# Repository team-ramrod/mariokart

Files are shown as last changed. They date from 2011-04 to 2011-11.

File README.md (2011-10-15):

MarioKart
=========

The full description of this project can be found on our [github wiki](https://github.com/team-ramrod/mariokart/wiki)

Purpose
-------

To retrofit one of the EE department's electric go-karts with a drive by wire
system, controllable over a single USB interface. Add to this a simple example
of a closed-loop controller using sensors and software running on a \*nix
laptop.

Method
------

Control the electric motor, servo driven steering wheel and actuated brake
pedal via embedded arm microprocessors. The separate micros are connected via a
CAN and also leave room for an arbitrary number of analog and digital sensors.

Behavioural-level software runs on a laptop connected to this network via USB.

Future Work
-----------

Develop a more complete sensor network (possibly including computer vision in
collaboration with cosc428) alongside more advanced controller software.

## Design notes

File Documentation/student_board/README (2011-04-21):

This is the source code for the student board running a ATmega8 on the go kart.
It was given to us by Bill
It also includes the schematic for the pcb.

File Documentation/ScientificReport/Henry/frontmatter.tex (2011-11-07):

\title{Embedded Hardware Design For An Autonomous Electric Vehicle}

\author{
  \IEEEauthorblockN{
    Henry Jenkins \\
    \href{mailto:hvj10@uclive.ac.nz}{\texttt{hvj10@uclive.ac.nz}}
  }

  \vspace{0.5\baselineskip}

  \IEEEauthorblockN{
    \emph{Coauthors}: Simon Richards, Zachary Taylor, Wim Looman and Dr Andrew Bainbridge-Smith\\
    \href{mailto:scr52@uclive.ac.nz}{\texttt{scr52@uclive.ac.nz}}
    \href{mailto:zjt14@uclive.ac.nz}{\texttt{zjt14@uclive.ac.nz}}
    \href{mailto:wgl18@uclive.ac.nz}{\texttt{wgl18@uclive.ac.nz}}
    \\\href{mailto:andrew.bainbridge-smith@canterbury.ac.nz}{\texttt{andrew.bainbridge-smith@canterbury.ac.nz}}
  }

  \vspace{0.5\baselineskip}

  \IEEEauthorblockA{
    Department of Electrical and Computer Engineering\\
    University of Canterbury\\
    Christchurch, New Zealand
  }
}

\maketitle

\begin{abstract}
  This report details the design and production of a hardware platform to for
  an autonimous go-kart. The system includes seven printed circuit boards
  (PCBs).  Five of the PCBs communicate via a CAN bus to collect data and
  control other circuitry, while the other two PCBs control actuators for
  steering and brake control. The system is based around Atmel AT91SAM7XC micro
  controllers along with various other electronics. The PCBs built for this
  system  are four layers so were manufactured in America by Advanced Circuits,
  then populated and tested at the University of Canterbury.
\end{abstract}

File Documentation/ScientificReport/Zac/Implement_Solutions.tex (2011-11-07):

\section{Implementation of Solutions}

Colour detection, SURF and chessboard detection were all implemented to evaluate their performance for tracking a marker in the required environment. To aid in this implementation extensive use was made of the Opencv computer vision libraries \cite{opencv}. These libraries were used as they contained implementations of a large number of computer vision algorithms that had been thoroughly tested by a large community and optimized to run as effectively and efficiently as possible.

The first algorithm implemented was the simple colour based approach. In this approach a bright blue ball was used as the marker to track. Initially the scene was thresholded for a value that was approximately a bright blue and opening (that is erosion followed by dilation) was used to fill any holes in the image of the ball and remove background noise. The output of this process can be seen in Figure~\ref{ball}. A rough estimation of the balls location was then made using its x and y position in pixels from the centre of the camera. The z location of the ball was taken to be proportional to the inverse of the square root of the size of the ball in pixels. These measures of x, y and z were extremely crude however they provided adequate for the testing that was performed on the colour method.

\begin{figure}[ht]
	\begin{center}
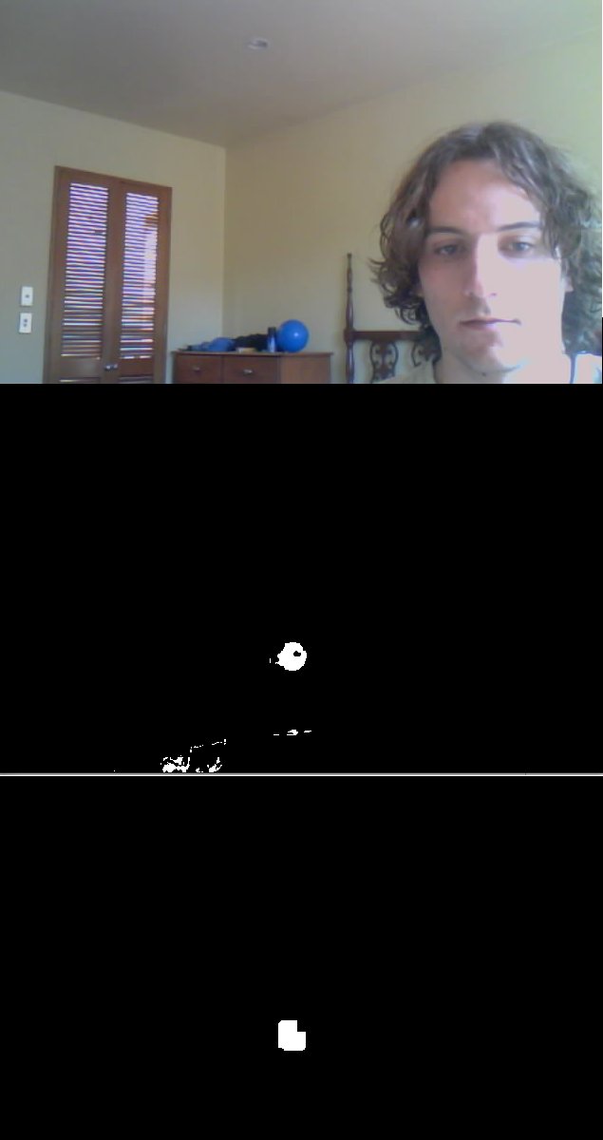
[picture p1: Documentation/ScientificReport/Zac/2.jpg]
		
	\end{center}
	\caption{Detection of marker ball using colour}
	\label{ball}
\end{figure}

For both the SURF and chessboard algorithms the intrinsic parameters of the camera had to be found so that the size of an object on the screen could be translated from the arbitrary pixel co-ordinate system used by the images to real world distances. These parameters were found by using the camera to take a series of photos of the chessboard from different angles and distances and using the geometry of the chessboard to extract the cameras parameters \cite{cali}. Once this had been performed the parameters were saved to a file that was used by both algorithms. This calibration was a small disadvantage of these algorithms however as it only had to be performed once for a web-cam it did not diminish the practicality of their use by much.

The SURF algorithms marker was a printout of a cut away of an aeroplane. This image was used as it contained a large amount of strong lines and detail that meant that a large number of unique and easily identifiable points could be located on the image. An example of the SURF algorithm working can be seen in Figure~\ref{plane}. 

Two chessboards were constructed and tested with the chessboard registration algorithm. A large 6 by 5 chessboard with 100 mm squares and a smaller 7 by 8 chessboard. The larger chessboard was to be used with the kart once it was running. The smaller one was used for calibrating the camera and the testing covered in this report. The smaller board can be seen being used in Figure~\ref{tracking}. 

\begin{figure}[ht]
	\begin{center}
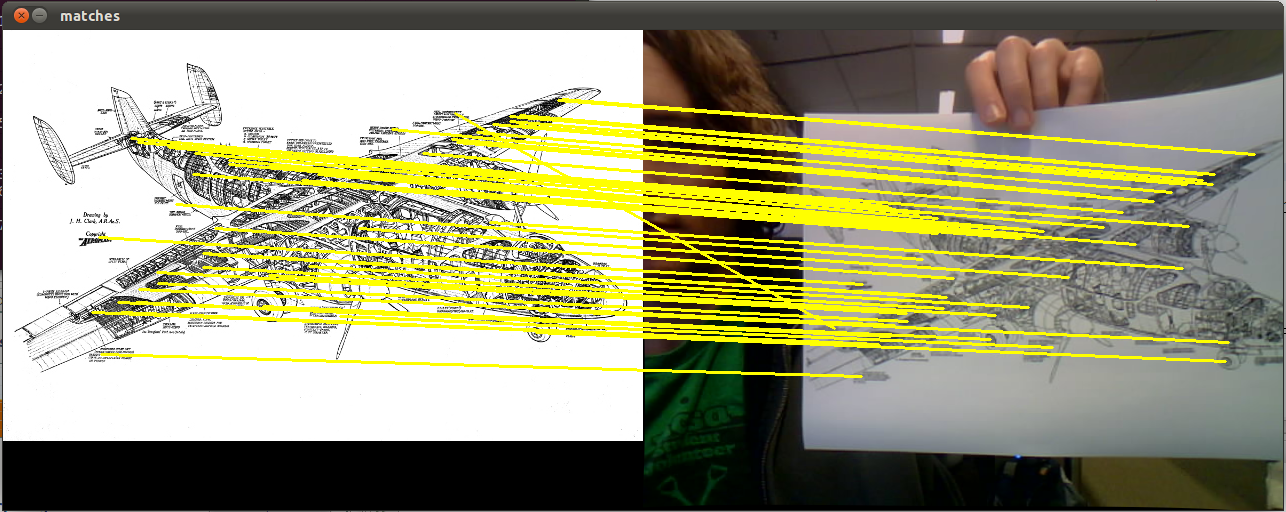
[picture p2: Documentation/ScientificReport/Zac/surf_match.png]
		
	\end{center}
	\caption{The SURF algorithm matching points in the marker image to the scene}
	\label{plane}
\end{figure}

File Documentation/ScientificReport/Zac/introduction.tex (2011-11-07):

\section{Introduction}

An electric go-kart was to be converted to allow it to navigate autonomously. To this end the system, nicknamed Mariokart was being modified so that it could be controlled from a laptop. This control system required a program to be written which would give the kart some basic autonomous functionality. This program was to function as a proof of concept of the kart's abilities as well as a method to test the systems that had been added to the kart. It had been decided that this program should allow the kart to follow a marker. 

The system that was being designed allowed the systems on the kart to interface through a laptop to 5 boards located on different areas of the kart. These boards handled all the low level control of the kart providing the laptop with functions to set the steering, brake and accelerator position. It also provided functions to access sensors located on the kart through fairly high level commands. The only sensor present on the kart at the start of the development was a speed sensor however a large number of I/O ports of different types allowed for the addition of extra sensors.  

The developed program was to run on the on-board laptop. It had to operate in real time recognizing the marker, finding its location and outputting the path to travel on with minimal lag. The kart was expected to be able to operate in both indoor and outdoor environments in a large variety of conditions without losing the marker. The system and any additional equipment and sensors required had to be low budget as the total budget for the entire conversion was less than \$1500.

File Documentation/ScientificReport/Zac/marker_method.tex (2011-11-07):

\section{Marker Location Methods}

A large variety of location methods were looked at when determining what type of sensors should be purchased for the kart system. Most modern autonomous vehicles rely heavily on scanning laser sensors as their main method of viewing the surroundings. Scanning lasers as their name implies rapidly move a measuring laser over the environment forming a matrix of distances to provide a 3D view of the world \cite{laser}. While these lasers are extremely useful they were discounted as a possibility early due to their high price tag with even the most basic models starting at \$2000. The Microsoft Kinect camera was briefly looked at as an alternative solution that would provide 3D information about the world \cite{kinect}. This camera uses structured light combined with an IR (inferred) camera to detect the location of objects in its field of view. This system was also quickly discounted however as it had a maximum range of only 3.5m which was too limiting for the application of tracking a marker from on board a kart. A second aspect that counted against the Kinect was that the IR pattern used by it was washed out by direct sunlight making outdoor use impractical.

GPS systems, while briefly examined as a possibility were not given any serious consideration due to their inability to work reliably in an indoor environment. One solution that was given serious consideration was using a marker that output a RF (radio frequency) signal and having three RF receivers on the kart use the  relative strength of the signal to triangulate the position of the marker. After further research it was found however that distance estimation using the level of RF detectors that were within the budget was only accurate to around 1m under ideal conditions \cite{rf}. This limitation meant that the receivers would have to be placed far apart to minimize the effect the error would have on the direction the triangulation would calculate the signal to have come from. On a mobile kart system where the close proximity of the sensors was unavoidable this limitation made the method infeasible.

The sensor system that was decided upon to develop was a computer vision system. This system utilized a web-cam mounted to the front of the kart. A unique marker was to be used that could be located in the image. This method had several advantages over the other methods considered. It was a cheap and easy to mount solution with only a web-cam required that would attach straight to the laptop with a USB cable. It provided a large degree of flexibility with a large suite of different algorithms and methods able to be implemented and tested for no modifications to the hardware the system was using. Finally it was the only system that showed promise in being able to locate a marker accurately at distance and within the budget. It was for these reasons that the computer vision system was the only option pursued for development.

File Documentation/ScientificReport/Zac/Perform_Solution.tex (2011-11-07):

\section{Performance of Solutions}
The algorithms were put through a series of tests to guage how well they would perform in the system. All the tests were performed on a 2.1 GHz notebook with an Intel Centrino Duo processor. The webcam was a Creative Labs Laptop Integrated Webcam. This webcam had a resolution of 320 by 240 pixels and operated at 20 fps.

\subsection{Robustness to lighting}
The robustness to light was tested by setting up an algorithm to recognise its marker in a room with a large amount of natural light. The lighting was then changed by closing the curtains and seeing if the object was still detected, once this was done the rooms lights were turned on. Colour detection performed the worst in this test requiring recalibration before it could detect the target after every change in lighting. Its robustness could be improved but this caused issues with background noise, this is gone into in detail in subsection E. The issue  with lighting arose because while the hue of the marker being located remained constant changing the lighting levels altered the hue the camera perceived the marker to be by a small amount. This problem stemmed right from the fundamental method by which the camera detects light and so very little could be done without recalibrating to attempt to account for this change \cite{detect}. The SURF algorithm handled almost all lighting changes without issue. The one situation in which it failed was if enough glare was coming off the marker it was locating to completely obscurer most of the features it was trying to find. The chessboard algorithm worked under every tested lighting condition.

\subsection{Frame processing speed}
The FPS (frames per second) for each system was recorded under normal operation. The colour detection algorithm required easily the least processing power of all the computer vision methods looked at running at a solid 20 fps only limited by the speed of the camera it was receiving the images from. The SURF algorithm operated very slowly originally operating at 0.8 FPS on locating a 640 by 480 pixel reference image in the scene. This speed was increase to 2 FPS by decreasing the reference image to 320 by 240. This was the lowest quality reference image which could be reliably placed in the scene. Chessboard detection operated slowly if the chessboard had not been located in the previous frame only operating at a rate as low as 2 fps. Once the chessboard was found however the algorithm used the previous location to find it more quickly raising the frame rate to around 15 fps.

\subsection{Robustness to motion}
Robustness to motion was tested in a fairly subjective manner. The marker was held roughly 1m from the camera and shaken until detection was lost. With colour detection regardless of how fast the marker was moved detection was never lost, though the detected size decreased by up to around 50\% as the image of the marker became a blur. With SURF detection only slow and careful movements would prevent the camera losing the target. Chessboard detection would lose the board if any quick or jerky movements were made. While this test was quite crude it clearly showed that SURF would be too susceptible to motion blur to be appropriate. It also showed that chessboard detection was weak to it and a higher quality camera or some pre-processing might be needed to help reduce the effect of motion blur when the system is attached to the kart.

\subsection{Maximum distance for detection}
The maximum distance the algorithm could detect a marker from was tested next. To make this a fair test for all systems the marker size for each system was set to an A4 page with the colour detections blue ball replaced by a sheet of blue card. The test was performed by walking away from the camera holding the marker and recording the distance at which the target was lost for the first time. The process was repeated three times and the results shown in Table~\ref{dist}. SURF performed easily the poorest of the solutions with the marker needing to take up a large portion of the field of view of the camera before recognition occurred. The chessboard algorithm lost the board at around 3m. At this point the 2.5cm squares on the board were only around 3 pixels in height and so little more in terms of performance could be expected from the algorithm. The colour detection operated up to 10 m at which point the marker was so small on the camera that it was removed as noise during opening. All three algorithms only operated over a relatively short distance in comparison to how far the kart might be from the marker. This would mean that the actual marker to be tracked would need to be significantly larger then those used in testing and/or a higher resolution camera would have to be used.

\begin{table}
	\caption{Distance before detection of marker is lost (all values in meters).}
	\begin{center}
    	\begin{tabular}{ | l | l | l | l | l |}
    	\hline
    	Algorithm & Run 1 & Run 2 & Run 3 & Average \\ \hline
		Colour & 10 & 11.5 & 9 & 10.2 \\ \hline
		SURF & 1.0 & 0.7 & 1.1 & 0.9 \\ \hline
		Chessboard & 3.5 & 3.0 & 3.2 & 3.2 \\ \hline
    	\end{tabular}
	\end{center}
	\label{dist}
	
\end{table}

\subsection{Robustness to background noise}
The ability of the algorithm to operate on a variety of backgrounds was tested. How much the colour detection was effected was closely coupled to how well it performed in varying light. If the range of hues and saturations was set to be very close to the markers colour then almost no issues with background objects occurred. An example of this can be seen in Figure~\ref{ball} where the blue ball is detected while sitting next to a blue can and a blue towel with neither of these being detected. These close tolerances meant that lighting had to be kept almost constant for the marker to be detected. If these ranges were relaxed to work in more varying light then any similarly coloured part of the background would also be detected. The SURF algorithm also had issues with the background. When the image was being tracked a small amount of the points (usually less than 10\%) would be attributed to points in the background. These incorrect points did not affect the algorithm however as the RANSAC algorithm detected them for the outliers that they were. The main issues came when the image was far away, partly obscured or absent from the scene. In these situations a large number of points would be detected at locations in the background giving false positives for locations of the marker. These locations were almost always easy to detect as they usually claimed that the marker was hundreds of meters away however they still required filtering and subtracted from the robustness of SURF. The chessboard was almost completely unaffected by the background. This was because while on occasion a false corner point was detected as it did not match the structure of the rest of the points it was discarded without problem. This lead to no false positives as for a chessboard to be perceived when not present, 42 false points would have to be located in a structure that very closely resembeled that of the chessboard.

\subsection{Accuracy of distance measurement}
The accuracy of the distances given was tested by placing the marker at 3 different points and recording the error of the system. These measurements are shown in Table~\ref{acc}. The SURF detection performed poorly in this test having an average error of 18\%. It also failed to register on the 2 meters test performing easily the worst of the three. Chessboard detection was almost as accurate as the tape measure being used to compare the distances giving a maximum error of only 1.5\%. Colour detection performed far better than expected given its crude distance calculation method having an error of only 6.8\%. Something that must be taken into account however is that the colour detection is in reality less accurate then this test indicated. This is because the amount of the marker detected depends on the lighting conditions and the distance was calculated using size of the marker. This meant turning on a light could change the distance the process believed the marker was at by a large amount (20\% in one rough test).

\begin{table}
	\caption{Accuracy of distance measurements}
	\begin{center}
    	\begin{tabular}{ | p{1.1cm} | p{0.5cm} | p{0.6cm} | p{0.5cm} | p{0.6cm} | p{0.5cm} | p{0.6cm} | l |}
    	\hline
    	Algorithm & \multicolumn{2}{|c|}{At 0.5m} & \multicolumn{2}{|c|}{At 1m} & \multicolumn{2}{|c|}{At 2m} & Avg \\ \hline
    	& Value & Error & Value & Error & Value & Error & \\ \hline
		Colour & 0.57 & 14.0\% & 1.03 & 3.0\% & 2.07 & 3.5\% & 6.8\% \\ \hline
		SURF & 0.61 & 22.0\% & 1.14 & 14.0\% & - & - & 18.0\% \\ \hline
		Chessboard & 0.495 & 1.0\% & 0.99 & 1.0\% & 1.97 & 1.5\% & 1.2\% \\ \hline
    	\end{tabular}
	\end{center}
	
	\label{acc}
	
\end{table}

\subsection{Testing conclusions}
From these tests it was concluded that chessboard detection was the only algorithm that was appropriate for use on the kart. This was because SURF was too sensitive to motion blur and had too short a range for the application. While colour detection out performed chessboard detection in several areas its sensitivity to light changes meant that it would never be robust enough to be useful.

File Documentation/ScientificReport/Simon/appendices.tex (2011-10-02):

\section{Appendices}

\subsection{Promela examples}
Client Board proctype:
\lstinputlisting[language=Promela]{client.pml}

\pagebreak
Never claim: All boards transition to error state
or remain in running state indefinitely:
\lstinputlisting[language=Promela]{never.pml}

\subsection{Single board state machine}

\begin{figure}[!ht]
  \caption{The state machine each board follows.}
  \label{states}
  \centering
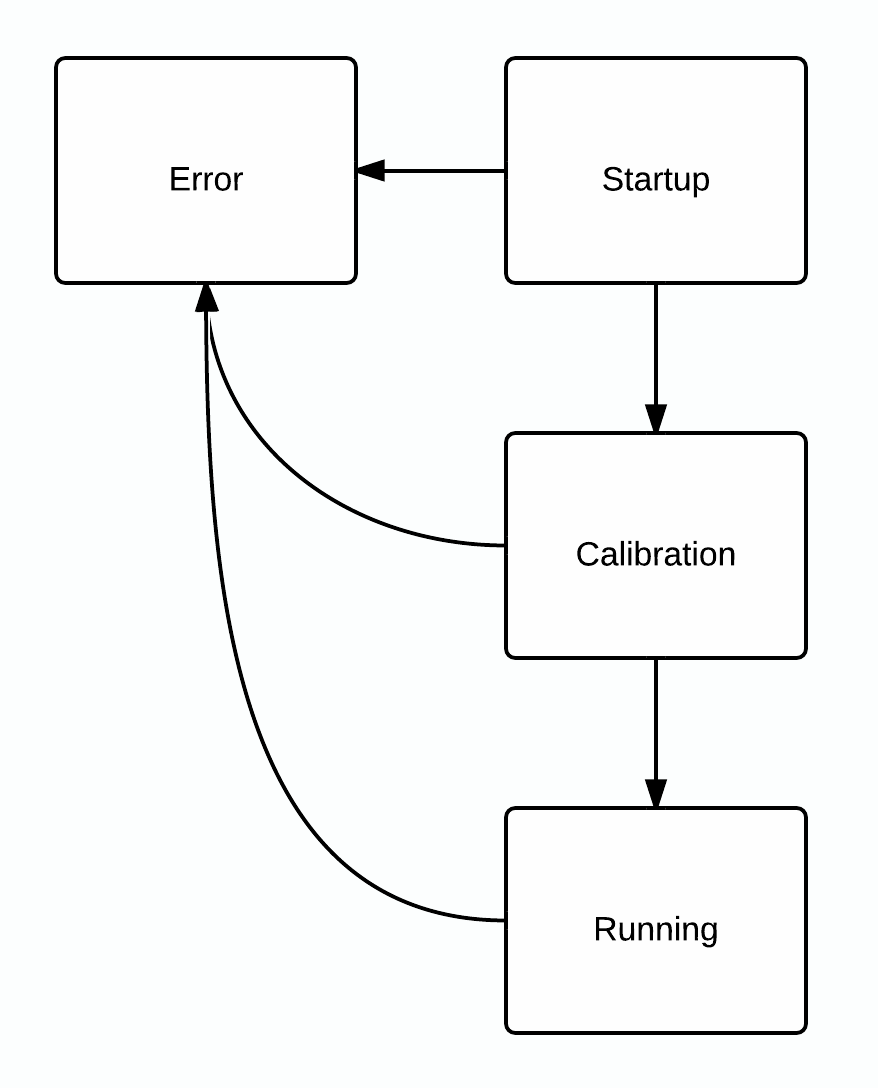
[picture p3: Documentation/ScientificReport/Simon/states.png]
    
\end{figure}

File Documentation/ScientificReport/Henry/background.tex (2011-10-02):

\section{Background}
  To interface to the go-kart, actuators were required to be placed at both the
  front of the kart, as well as interfacing to the power electronics in the
  rear.

\subsection{The Go-kart}
  The department has 5 electric go-karts that were purchased for the specific
  purpose of a assignment and project platform, one of these shown in Fig.
  \ref{go-kart}. Throughout the year several, mostly power electronics,
  assignments are based on the Junoir Sport JS80IIR go-kart\cite{go-kart}. These
  go-karts are 1.7 meters in length, can hold two passengers and came with a
  80cc petrol motor. The petrol motor has since been replaced with a DC electric
  motor and batteries.

  \begin{figure}[h]
      \centering
      
      \caption[Junoir Sport - JS80IIR go-kart]{Electrical and Computer
      Engineering go-kart}
      \label{go-kart}
  \end{figure}

\subsection{Power Supply}
  The go-kart has a single power source for the whole vehicle. Two lead-acid
  batteries provide power for the existing DC drive motor and power electronics.
  These batteries can handle large currents at a voltage ranging up to 26 volts.
  The batteries have also been made accessible to be used for the autonomous
  vehicle control system.

\subsection{Power Electronics}
  To control the DC Drive motor, the department has designed and built three
  PCBs to switch and regulate currents going through the motor. Figure
  \ref{powerE} shows the three PCBs, where from left to right they are known as
  the \emph{student board}, \emph{control safety board} and \emph{power
  electronics board}. The \emph{student board} is a 5V logic board that takes
  the position of the accelerator pedal, current sensor data and outputs a PWM
  signal for the \emph{control safety board}. The control safety board is there
  to make sure the \emph{power electronics board} is not incorrectly driven,
  which would damage the go-kart.

  \begin{figure}[h]
      \centering
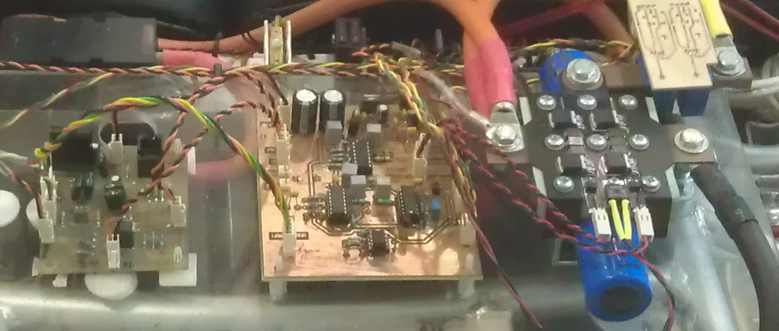
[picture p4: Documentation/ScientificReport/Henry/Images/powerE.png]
      
      \caption{Power and control electronics for go-karts DC motor}
      \label{powerE}
  \end{figure}

\subsection{Actuator Control}
  To control the steering position and apply the brakes two actuators were
  purchased for the project.

  \subsubsection{Steering}
    The steering motor is a 24V DC motor that has a step down gear box with an
    output ratio of 393:1. On the top end of the motor, there is a magnetic
    encoder\cite{encoder} that outputs 18 pulses per motor revolution. This is that it outputs
    7,074 pulses per 360 degrees of rotation on the steering wheel. At peak
    load, the steering motor can draw up to 10Amps continuously.

  \subsubsection{Brake}
    To control the position of the brake a linear actuator is used. The linear
    actuator has an extension of 101.6mm and can travel at 20mm/s. It provides
    absolute position feedback via a $10k\ohm$ potentiometer. As with the
    steering motor, the brake linear actuator ran at 24V but only draws a peak
    current of 1.3Amps.

\subsection{Communication With A Laptop}
  Because most laptops have dropped all serial RS-232 ports, the only reliable
  option for serial communications is to use USB.

\subsection{Schematic \& PCB design tools}
  To generate the PCBs and schematics, Altium Designer was used\cite{altium}.
  Altium Designer is a complex electronics design package that can be used from
  a variety of tasks. However in this project only the schematic layout and PCB
  design tools were used.

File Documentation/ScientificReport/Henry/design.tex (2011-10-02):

\section{Design}
  To avoid problems of running long signal wires, especially near the large DC
  go-kart motor, it was decided to distribute the electronic control hardware.
  This also has the benefit that the system is extensible including being able
  add new sensors later on with plenty of spare IO spread around the kart.

  To make the design simpler and cheaper the same design was used for all the
  main PCBs. Just not populating certain components where they are un-nessary.
  For example, the USB connector was only placed on the \emph{comms board} as it
  is the only board that requires to talk to a computer.

  \subsection{Board locations}
  To prevent long runs of digital logic in the go-kart there were five PCBs
  placed around the go-kart. The locations of the boards are:
  \begin{itemize}
  \item Steering - Placed where the steering wheel is, next to the steering
  actuator.
  \item Brake - Directly next to the brake actor where the brake pedal normally
  is.
  \item Comms - On the go-kart seat with the laptop next to it.
  \item Motor - Connected to the power electronics controlling the main DC motor
  \item Sensor - Near the rear axle collecting speed data from the inductance
  sensor.
  \end{itemize}
  Figure \ref{locations} shows a sketch of where the PCBs are located.

  \begin{figure}[h]
    \centering
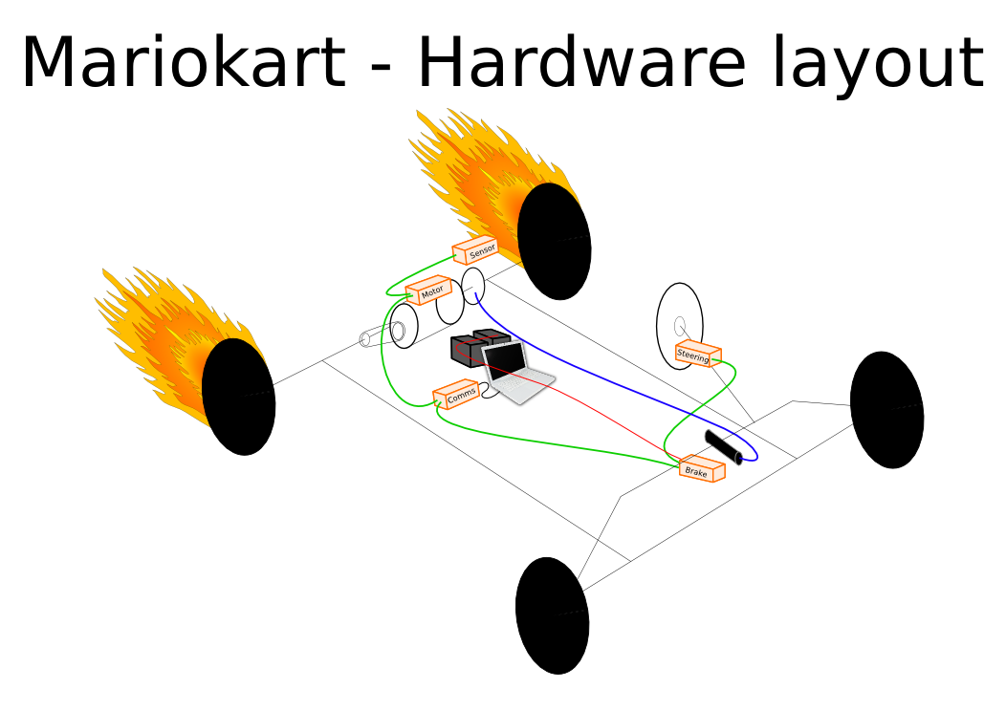
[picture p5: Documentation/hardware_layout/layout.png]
    
    \caption{Locations of PCBs for go-kart}
    \label{locations}
  \end{figure}

  \subsection{Communications Network}
  Because the go-kart was required to be controlled by distributed hardware,
  some way of having the hardware communicate was required. To solve this
  problem, Local Interconnect Network (LIN Bus), Controller Area Network (CAN
  Bus), Universal Asynchronous Receiver/Transmitter (UART) and Serial
  Peripheral Interface Bus (SPI) were evaluated as viable options. Both LIN and
  CAN are serial communication buses designed for use in vehicle and automation
  systems, where UART and SPI are designed as simple serial communications.
  
  \begin{itemize}
    \item[LIN]{LIN is a single wire communications standard which supports
    speeds of up to 19.2kbit/s\cite{LIN}. It is a master slave design which
    supports up to sixteen slaves. The data frame on the LIN Bus is variable
    length of either 2, 4 or 8 bytes. There is no collision detection, however
    data checksumming and error detection is implemented in the standard.  LIN
    was designed in 1999 with further LIN standards released in 2002 and 2003.}

    \item[CAN]{CAN 2.0 is a master-master broadcast serial bus standard. It
    supports half-duplex data rates of up to 1Mbit/s. The CAN Bus uses a
    differential pair with the traffic encoded in non return to zero. Each
    packet is formatted with a header, including receivers address, followed by
    zero to eight bytes of data. Robert Bosch GmbH \cite{bosch} developed the
    standard in 1983, but now days the ISO11989 standard also describes CAN 2.0
    \cite{boschCAN, ISOCAN}.}

    \item[UART]{Using UART was dropped as an idea rather early on. This is
    because it does not support the error correction that was needed for the
    project. Another area it was lacking is being expandable. A new UART would
    be required for each new node or device.}

    \item[SPI]{For much the same reasons UART was not used for our central
    communications bus, SPI was also not appropriate.} 

  \end{itemize}

  It was decided that using a CAN Bus would be the best option. Some major
  factors that influenced this choice over LIN were; the CAN standard had better
  documentation, more nodes can be added to the network later on with little
  extra effort, hardware level collision and error detection and CAN controller
  supported by Atmel SAM7 series micro controller. Atmel also provided a CAN
  transceiver IC\cite{ata666}, however this could have been replaced by a IC
  made by Texas Instruments\cite{ti-can-trans}.

  Although both UART and SPI were not used for the system bus, both can be used
  for local sensors, or other expansion modules.

  \subsection{Micro Controller}
  The main requirements of the micro controller are that it supports both a CAN
  controller and hardware USB. Also because previous projects had used either
  the Atmel ATMega or the Atmel AT91SAM7 micro controllers, it was of preference
  to use these rather than learning a new architecture and data sheet format.

  \subsection{Motor Drivers}
  To drive the actuators for the steering and brake we decided to use a motor
  driver IC. By basing our motor driver circuit specification on the current
  draw of the steering motor, then reused the same design for the brake linear
  actuator we could use the same circuit for both actuators. This was done both
  to save time in the hardware design, but also time in software later
  on\cite{Looman_2011}. The motor driver circuits were placed on their own small
  PCB to save space on the main PCBs and also provide more opportunity for heat
  dissipation if this were to become a problem. 

  The motor driver that was used is the DRV8432 made by Texas
  Instruments\cite{ti-motor-driver}. It is a dual full bridge PWM motor driver.
  It has a split logic and driving voltage, so it is driven directly from the
  batteries, but the control logic is at 3.3V. It has a peak voltage of 50V and
  a maximum current of 12A which is more than we need for either of the
  actuators. Figure \ref{motorPCB} shows one of the two motor driver boards with
  a heat sink covering the motor driver IC.

   \begin{figure}[h]
     \centering
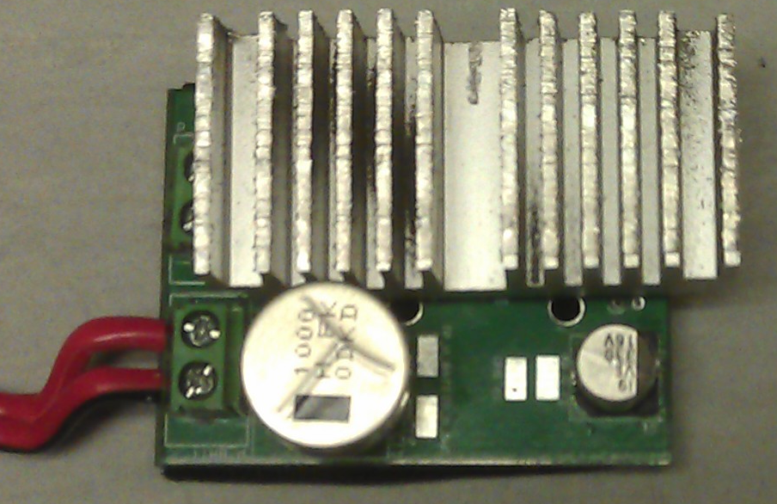
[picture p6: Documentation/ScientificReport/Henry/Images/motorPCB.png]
     
     \caption{Motor driver board for driving actuators}
     \label{motorPCB}
   \end{figure}

  \subsection{Expansion IO}
  To allow the hardware to be expandable, two 3.3V UARTs, one 3.3V SPI and
  one 5V logic SPI are exposed on each PCB. Each serial port has it's own
  PicoBlade connector\cite{PicoBlade} as well as all the power supplies are
  exposed via another connector. All the serial port pins can also be set to be
  GPIO to allow them to be used for other purposes too.

  The 5V logic SPI is enabled via the use of a logic level shifter chip
  the MAX3001E made by Maxim \cite{MAX3001E}. To complement the 5V spi, a 5V
  external ADC is also on the boards. This was placed on the boards for the
  purpose of replacing the student board, but can be used for other analogue
  input too.

  \subsection{Encoder Reading}
  Because getting both speed and directions from an encoder signal in software
  is quite tricky, a quadrature clock converter was placed on the main steering
  PCB.  This takes in the encoder pulses and out puts a single pulse and which
  direction it is rotating in. Which allows a simple counter and incrementing or
  de-incrementing it to keep the actuators position.

  \subsection{Debugging}
  To make debugging easier, epically in the early stages of development, a two
  digit seven segment display and 4 push buttons are placed on each main PCB. The
  display is driven by a display driver. This display driver takes a four bit
  number in parallel and converts it into the segment array lines. It is
  multiplexed with the second segment so by switching between the displays
  faster than 20Hz allows both digits can be used.

  \subsection{On Board Power}
  On each board there is four different voltage five levels. There is the
  battery voltage, which is only used by the voltage regulators, 3.3V, 5V, 12V
  and ground. Because we used a 4 layer PCB design, excluding the battery
  voltage, each of the voltage levels were spread across a whole plane on the
  PCB allowing better coupling between them and ground.

    \subsubsection{3.3 Volts}
    This was used by most of the logic components including the SAM7 micro
    controller. As less than 300mA was required and having a smooth, non-rippled,
    voltage would ensure the micro controller ran well, a linear voltage
    regulator was used.

    \subsubsection{5 Volts}
    The main reason for having 5 volts on the boards was to allow a 3.3V to 5V
    logic translator to be used. This level shifter is required by the student
    board in the power electronics. A linear voltage regulator was used here
    also.

    \subsubsection{12 Volts}
    Both the inductance sensor, which is used for speed detection, and the motor
    driver required 12 volts. Both of these applications use less than 150mA so
    a Texas Instruments TPS7A4901 linear voltage regulator was
    used \cite{TPS7A4901}.

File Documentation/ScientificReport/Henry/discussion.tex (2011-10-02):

\section{Discussion}
 In general the design process produced good stable and usable boards. However
 there were a few areas that needed improving on.

\subsection{Debug Port}
  When the schematic was being set out the debug unit from the SAM7 were left
  with no header leading to them. At the time it was thought that they would be
  unnecessary and then were forgotten about. This meant all the debugging was
  required to be done via a UART port and the display. While this wasn't a bad
  solution to the problem, it would have been better to have access to the debug
  unit.

\subsection{Test points}
  At the last minute in the PCB design about 100 test points were added to the
  bottom of the PCB. This was very useful and one of the better design decisions
  with the PCB. The test points gave access to many different signals on the
  board with test point probes able to be clipped onto them. The only thing that
  should be done differently with the test points is placing more ground test
  points around the board. This would allow more than one oscilloscope cable to
  be hooked up to the ground on the board.

\subsection{Power Supply Selector}
  Making the decision to put battery voltage over the same cables that the CAN
  bus uses made the system work well. However when developing and debugging, it
  would have been ideal to be able to disconnect the power coming in from the
  CAN bus cable. This would mean that an individual board could be power cycled
  without having to power cycle all of them. This could have been done by simply
  putting two jumpers on the PCBs to connect specific ones to enable either the
  CAN bus power or the battery header power.

\subsection{Connectors}
  To save space the Molex Pico Blade \cite{PicoBlade} connectors were used.
  However after using them this was a bad choice. They are very hard to make
  cables for, then brake a short time after. This is frustrating when it takes
  so long to make them, yet they don't last long. While using bigger more
  traditional connectors would have taken up more space on the PCBs, it would
  have saved a lot of time while developing with the boards.

%\subsection{Atmel Library}
  % You suck atmel

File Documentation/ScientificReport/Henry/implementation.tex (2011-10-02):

\section{Implementation}
  The Main PCBs are four layer PCBs that were designed using Altium software.
  They are approximately 120mm long by 60mm wide.

  \subsection{Schematics}
  Using Altium Designer the schematics were laid out. Two techniques were used
  to minimise mistakes in the PCB design. One was to divide all the schematic
  sections onto separate sheets. The other was to be methodical and make notes
  on the sheets if something was not complete. Part of being methodical also
  meant making sure all components were well labelled, even some with comments
  next to them to help explain their existence. This meant when the schematics
  were printed off and reviewed by the whole team, mistakes could be easily
  spotted.
  
  \begin{figure*}[h]
      \centering
      
      \caption{Top level schematic for the main PCB.}
      \label{main-schematic}
  \end{figure*}

  Figure \ref{main-schematic} shows the top level schematic with the MCU in the
  middle of the page. The green boxes on the sheet show where other sub sheets
  have been included and wired up. For example, doing this all the decoupling
  capacitors for the micro controller are essentially hidden in one of these
  sub sheets. 

  \subsection{PCB Design}
  The PCB layout design work was also done in Altium Designer. While the tool
  does not automatically do the layout for the user, it does provides many
  useful tools to aid the process. By setting up the design rules to match the
  manufactures specifications, the manufacture process is sped up eliminating
  them rejecting your design because of design rule violations.

  The main technique that was used when laying out the PCB was to arrange
  clusters of components that are all related. Then place these modules on the
  PCB area. This also allowed the placing of decoupling capacitors in the
  correct locations next to the pin that required the decoupling.
  
  One key rule that was stuck to when laying the PCB was to only put small
  components on the bottom. This allowed the population of the whole bottom side
  of the PCBs then when populating the top side, the components would not fall
  off the bottom in the oven. It also meant we could fit the PCBs in the lid of
  the enclosure that we designed the boards to fit in. The small resistors and
  capacitors don't even touch the inside of the lid.

  \subsection{Components}
  Where possible surface mount technology (SMT) components were selected. This
  has the benefit that it minimises the amount of drilling required to be done
  by the manufacturer. It is also easier to source SMT components. In the final
  design only some connectors are non-SMT.

  \subsection{PCB Manufacture}
  To allow four layer PCBs to be used, the PCBs needed to be manufactured
  off-shore. Because of recommendations by staff in the department, either
  Advanced Circuits in America\cite{advancedCircuits} or OurPCB Tech in
  China\cite{ourPCB} were our best options.  Because of price, Advanced Circuits
  were used. All up for 3 panels, which included all 5 main PCBs and two motor
  driver daughter boards, the charge was 362 USD including shipping. The panels
  were manually cut into the individual PCBs, using a band saw.
  
  \subsection{PCB Population}
  Component population was done initially using a PCB oven, then
  reverting back to hand soldering once the bulk of the components were on the
  PCBs. Population was done in stages, to allow testing of the boards at each
  stage. Figure \ref{fullPCB} shows the brake PCB with all it's components on
  it.
  
  \begin{figure}[h]
      \centering
      
      \caption{The populated brake PCB}
      \label{fullPCB}
  \end{figure}

  \subsection{Hardware Testing}
  Before the PCBs even had any components put on them they were tested for
  manufacturing and design flaws. Simply using a multi meter, checking to make
  sure the power planes were not shorted and other key pads were connected as
  they should have been. Then continued to be tested at every stage especially
  making sure the power and ground planes were not shorted was a key concept. At
  several stages shorted pins were picked up because of this testing.

  Once the PCBs had their micro controller placed on its PCB, led test code was
  written to ensure we were able to program and control the board. This also
  helped to pick up shoddy soldering on a couple of the micro controllers. The
  same was repeted for the CAN Bus, push buttons and USB.

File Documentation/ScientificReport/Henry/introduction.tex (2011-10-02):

\section{Introduction}
% Goal / problem statement (what is your goal/what problem are you solving)
  Currently the department of Electrical and Computer Engineering at the
  University of Canterbury has several go-karts. These go-karts were purchased
  as petrol go-karts then retrofitted with control electronics, power
  electronics, lead-acid batteries and a DC electric motor. The goal of this
  project was to take one of these existing electric go-karts and have it drive
  it's self autonomously. 

  An autonomous vehicle is a driver-less vehicle that is able to navigate from
  one location to another set location by controlling actuators and motors. This
  is achieved by gathering data from the surrounding environment in order to
  find and track the vehicle's current location. While the vehicle can have
  communications off the vehicle, like off loading signal processing, it is
  ideal to have the vehicle completely self contained. This, however, does not
  dismiss using incoming radio signals. For example using Global Positioning
  System (GPS) would be perfectly acceptable.

  The control systems, both mechanical and electrical, must interface with
  existing hardware on the go-kart. The project aimed to select appropriate
  actuators, motion and distance sensors, develop a navigation system, interface
  to the existing control systems and interface to a central computing platform.
  As the kart also was required for other projects, it was also a requirement to
  able return the kart to it's initial electric go-kart state within an hour.

  To be able to drive a go-kart autonomously, first the kart must be able drive
  according to given digital instructions. So the initial milestone is to build
  embedded hardware systems that is able to control the go-kart's main motor and
  drive actuators for both the brake and steering. Because the time line of this
  project spans approximately only 24 weeks, a sub-goal was set of having
  \emph{drive-by-wire} go-kart by the end of the project.

  To allow high performance, high level signal processing the control system
  must be able interface to a computer based platform. This platform will be
  able to run processor intensive tasks, like image processing for computer
  vision\cite{openCV}, or a Bayes filter for estimating the kart's current
  location before it receives accurate sensor data.

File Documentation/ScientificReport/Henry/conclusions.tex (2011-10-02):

\section{Conclusions}
  The design process used for the schematic and PCB layout worked well providing
  a set of very functional and reliable PCBs. They have been shown to all
  communicate together via the CAN Bus protocol and drive both the steering and
  brake actuators. 

  Since the project has been in the software development stage for some time
  now, there have only been three mistakes in the hardware found. All of these
  mistakes have had relatively easy fixes. The worst of the three is one side of
  the quadrature clock converter's pins were reversed. This was fixed by
  soldering the IC on upside down and then wiring the pins over to the correct
  pins. The second worst was a miss placed decoupling capacitor on the
  \emph{avref} pin of the SAM7. This was simply replaced with a zero ohm
  resistor to solve the problem. The third problem was that the UART connectors
  don't have a ground pin. To get around this the \emph{sclk} pin in tied low in
  software to act as a ground.

  Using the same design for all of the five main PCBs worked well. Doing this
  saved time in the design, ordering and population. This also saved money by
  being able panellise the boards which would have cost 50 USD more if wasn't
  done. By not having to spend time on making five different designs, more time
  was able to be spent checking for mistakes in the design. If there were
  multiple designs more mistakes would have happened.

  The CAN Bus produced clean signals with all nodes connected. Even with the CAN
  bus running at 1Mb/s its maximum speed. While the bandwidth of the CAN Bus is
  about 1000 times more than required for the current application of a
  drive-by-wire go-kart, it does mean the CAN bus can be expanded for future
  use with sensors and other devices generating traffic on the network. If noise
  were to become a problem, the bus is able to run at a slower rate potentially
  solving this issue.
  \newpage

  The help received from Michael Cusdin made this project possible. His
  knowledge and experience guided us through the PCB population process. Also
  technical knowledge provided by Dr Michael Hayes often lead us out of strife
  with challenging problems.

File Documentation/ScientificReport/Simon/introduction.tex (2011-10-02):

\begin{abstract}
An electric go-kart is outfitted with a drive-by-wire system in the first phase of development of 
an autonomous vehicle. The safety aspects of the design are evaluated and analysed  
using typical project management techniques. A model of the distributed software required is 
developed and proven and the place of modelling in software engineering is discussed..
\end{abstract}

\section{Introduction}

\subsection{Project Description}

The authors' reports are based on a group project carried out in the final year 
of their Bachelor of Engineering degree at Canterbury University. The original goal 
of this project was to take one of the electric go-karts used by the department for
power electronics projects and convert it into an autonomous vehicle capable of
a simple navigation task. Due to time restrictions the aim was reduced to implementing
the mechanical and electronic systems needed to control the kart's motion over a USB link.

The authors refer to the project using the moniker Mariokart and this name may be used 
throughout this report in reference to the team, the vehicle or the project itself.

\subsection{System Design}
The overall system design consisted of a laptop, electronics, a CAN bus, actuators and an interface to 
the existing motor driver  hardware.

\begin{itemize}
 \item Electronics: Five PCBs were located around the kart, each in close proximity to 
 the sub-system it was responsible for. The PCBs were identical in layout, specialisation was
 achieved by removing components from boards where they were not needed. For example
 it was intended for only one board to communicate directly with a laptop and so the other
 boards did not have USB headers. The decision to distribute control was made primarily to avoid
 problems caused by driving motors and actuators over a long distance in a high noise environment.
 \item Actuators: The brake pads were driven by a linear actuator mounted in place of the brake pedal. 
 The actuator was mounted to the floor of the go-kart and its driver board was situated nearby. The 
 steering column was similarly controlled by a DC motor mounted in place of the steering wheel 
 and fixed to the frame. The DC motor included an encoder so that the relative angle of the 
 steering column could be determined. Limit switches at each extreme of rotation ensures the
 motor does not turn too far and allows for the absolute angle to be measured.
 \item Controller laptop: To simplify use for future projects, the entire system is controllable via
 commands sent over a USB cable. The communications board is responsible for interfacing with
 a laptop and distributing the user's commands 
 
 \item Motor interface: Power electronics and a motor driver had already been implemented as part 
 of a student project so the only requirement from the motor driver board was to interface with this over
 the available SPI link.

 \item The CAN bus: CAN is a multi-master serial bus with guaranteed sending and message priority. It 
 was designed by Robert Bosch GmBH for networking micro-controllers in automobiles and has
 also some popularity in industrial automation. The CAN specification is low-level only, it does not specify 
 a data protocol or a method address allocation. There are numerous similar software stacks built on top
 of CAN for various purposes such as the Society of Automotive Engineers' J1939\cite{J1939} however due to the simplistic nature of our 
 network we implemented our own protocol.
\end{itemize}

For a more detailed description and justifications see \emph{Embedded Hardware Design For Autonomous Electric
Vehicle} \cite{jenkins_2011}.

\subsection{Risk}
As with any vehicle, autonomous or otherwise, there is always a risk to the user, bystanders and
 the go-kart itself if a part of the system malfunctions in any way. Replacing a human driver with 
 electromechanical control systems removes the non-deterministic element of human error 
 from the system but adds a new set of risks and potential design mistakes.
 
 In this paper, the sources of these risks will be listed analysed and techniques for mitigation and
 negation will be investigated and evaluated.

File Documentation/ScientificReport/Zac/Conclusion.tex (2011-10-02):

\section{Conclusion}

Three computer vision solutions were looked at for tracking a marker for use in allowing a kart to follow a lead vehicle. Colour detection was found to be light weight, robust to movement and reasonably accurate in constant lighting (error of less than 7\%). It was however plagued by a large sensitivity to lighting changes that made it unusable as a robust marker location system. The SURF algorithm ran slowly and its inability to handle distances over 1m and even small amounts of motion blur made it inappropriate for the application of being mounted to a moving vehicle. Chessboard detection was the only system that was robust enough to detect a marker and give its position reliability. It was slightly hindered by it inability to deal with large amounts of motion blur and large distances. The output of these systems were combined with sensors measuring the speed and wheel angle of the kart to produce a system that followed the path the marker had taken rather than just driving at the marker giving an accurate following method that could in the tests conducted effectively follow a marker placed on a leading vehicle. This following method was never tested on the kart however due to the kart’s drive by wire systems not being finished before the end of the project.

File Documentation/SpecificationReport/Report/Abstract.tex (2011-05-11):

\begin{center}\section*{Abstract}\end{center}
\thispagestyle{empty}

This project looks at transforming an electrically powered, mechanically controlled go-kart into an autonomous vehicle capable of driving and navigating without human assistance. We have three main goals for this project. The first is to integrate a drive by wire system into the go-kart, so that it can be easily controlled by a laptop. The second is to develop a set of libraries and example applications that makes use of on-board sensors and the drive by wire system to execute a simple autonomous algorithm. This algorithm will follow a marker allowing the kart to automatically follow a person or vehicle. Finally while we wish to progress further and develop a program that will allow the kart to detect obstacles and navigate between GPS points we believe that we will not have sufficient time to make any significant progress towards this final goal. To date we have developed schematics and detailed plans for the drive by wire system. We have begun to order parts and will begin putting together the systems in the next few weeks.

\vfill
  \begin{figure}[h]
    \centering
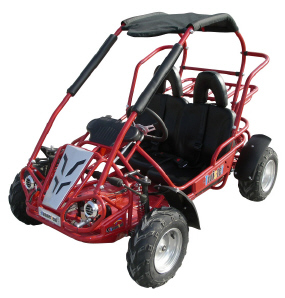
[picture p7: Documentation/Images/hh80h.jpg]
    
    \label{gokart}
  \end{figure}

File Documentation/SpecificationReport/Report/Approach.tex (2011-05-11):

\chapter{Approach and Preliminary Design}

\section{Approach}
Soon after receiving this project it was decided that we would break the project up into a series of smaller projects that we would complete in series. This decision was made after we realised that the transformation of the provided go-kart to a fully working autonomous vehicle was a goal that we would be unlikely to achieve in the time allotted.

If we start all of the sub-systems in parallel then it is likely that by the final deadline we would have many incomplete subsystems putting a steep learning curve in front of any continuation of our work.

By dividing the project into a series of modules with simple well documented interfaces between each we will ensure that we leave a single clean interface with which any future team can build upon with minimal repetition of work. The sub-projects we have divided this project into are outlined below
\begin{description}
\item[Drive by wire] This is the conversion of the go-kart from a traditional mechanical system to something that can be controlled by a laptop. 

\item[Sensor interfacing] In this module the sensors the system will use to perceive the kart's state and the world around it are chosen. After selection they will be attached to the kart and interfaced with the control system. 

\item[High level control of systems] The drive by wire module will provide kinematic control of the kart's speed and turning angle abstracting away low level control from the behavioural layer. An example of this abstraction is using the brake, accelerator and the Hall Effect velocity sensor to implement a closed loop controller for the kart's speed.  

\item[Simple autonomous behaviour] This stage is the development of a simple to implement program for autonomous control of the kart. For example using radio triangulation or computer vision to track a token so that the go-kart can autonomously follow a person or another vehicle.

\item[Complex autonomous behaviour] This module would see the integration of reactive path finding using distance sensors and absolute positioning using GPS into the autonomous go-kart's system. These will enable it to operate as a fully-fledged autonomous vehicle able to operate without any form of human interaction or control. When completed the go-kart will be capable of autonomously navigating to a GPS location whilst safely avoiding obstacles along the way.
\end{description}

\section{Safety}

As was outlined in the goals the kart has the potential to cause serious harm if the system fails to operate correctly. Because of this we have placed protocols in our design process to ensure that the go-kart is a safe system. The microcontroller controlling the accelerator will be configured so that it will never send a value to the accelerator that will allow the go-kart to travel at speeds greater then 10 kmph.

The microcontroller controlling the brake will apply the brake unless a signal is received periodically telling it not to. This will ensure that if the CAN bus fails or the control system computer stops responding that the brakes will immediately be applied. A similar system will ensure the accelerator is also off in this situation. In the event that the brake microcontroller fails to respond the control system will immediately disable the accelerator.

During initial software testing the kart's motor will be disabled, followed by testing with the kart placed on blocks so that its wheels do not touch the ground. This will allow us to thoroughly test all systems and most combinations of inputs without the kart moving or having any potential to lose control and crash. Once this testing is complete and during all future testing somebody will always ride in the karts passenger seat prepared to hit the emergency motor kill switch if the behaviour of the kart does not follow match expectations.

The linear actuator is almost entirely enclosed and moves only small distances, thus it requires no form of guard. The gear motor while slow moving has such a high turning force it has the ability to cause serious harm. Because of this the shaft attaching it to the pinion driving the shaft will be encased to prevent potential harm.

\section{Braking System}

The go-kart's brakes will be controlled via a linear actuator. This will be
connected by removing the brake pedal and connecting the actuator directly to
the input of the hydraulic brake systems. It was decided to use the existing
hydraulic system rather than attach a controlled actuator directly to the brake
disk. This was done as it allowed the system to be attached and operated with
minimal modifications to the existing kart. Another reason this decision was
made is that actuators with relatively low force and large travel were much more
readily available and cheaper then those with small movement and high force and
the existing hydraulic system already converted this large movement into the
high force required resulting in a cheaper system. Through rough testing it was
determined that a human could apply approximately 300 N to the brake pedal. The
leverage in the brake pedal was estimated at be roughly a 2 to 1 system. This
meant the ideal actuator had to provide 600 N of force to operate the brakes. To
go from full off to fully on the actuator required 30 mm of travel.

The actuator selected to power the brake was a 24V Warner linear m-track1. Its
specifications deviated from our requirements slightly. The actuator had 100mm
of travel more then three times the required making it longer then necessary.
However space was not an issue so this was not seen as a problem. The actuator
could only produce 450 N of force, it has yet to be seen how fast a deceleration
this will allow however as 600N is the maximum a human could reasonably apply we
are confident 450N will be sufficient. In the unlikely event this force proves
too small in testing the large travel of the actuator means it can instead be
mounted to the brake pedal using the leverage to give the required force. The
actuator moves at 15mm per second under load. This means that from off to full
lock takes 2 seconds. This speed is a lot slower then desired however the brake
pads do not actually touch the brake during the first half of the travel. This
dead zone is there to prevent drivers accidentally applying the brakes and to
accommodate different thickness brake pads as they wear. If the servo is
recalibrated on a regular bases this dead zone can be all but removed allowing
full brake control in a second. The main driving decision in the purchase of the
actuator was price. The actuator was an end of line product that had been
heavily discounted to sell this meant that it only cost \$110 NZD including
shipping to New Zealand from America. An actuator of similar specification could
not be located for less then \$220 in the US or within New Zealand for less then
\$300.

\section{Steering System}

The steering on the go-kart operates on a rack and pinion system. The steering
wheel rotates from lock to lock in 270 degrees. At rest on concrete the wheel
requires 7 Nm to turn, this value represents a worst case scenario with
significantly less force required when the kart is moving or on grass. Initially
a servo was going to be used to drive the steering wheel however servos with the
ability to produce 7Nm of continuous torque at a reasonable speed were found to
be both difficult to locate and prohibitively expensive (\$500+). Instead a
system of a DC motor, gearbox and encoder is to be used. For the motor to be
attached the steering column will be removed and the output of the gearbox
will drive the pinion directly with the motor bolted in the space left by the
removed column. %Not necessarily but it reads well.

The motor system selected for use in the go-kart is the IG52-04 52mm gear motor.
It comes with a 1:353 gearbox and a Hall Effect encoder attached to a second
rear output shaft on the motor. This motor was selected as it combined all the
required system into one convenient system which required no assembly on our part.
Another major reason for its selection was the large difficulty that was
encountered in finding any reasonably priced gearbox that could sustain the
continuous torque requirements of the system. This motor produces 10 Nm of continuous torque
which will allow it to easily turn the wheel. Its gearbox output rotates at 10
RPM allowing it to travel from lock to lock in 4.5 seconds. A concern with using
this motor is that it has the ability when stalled to produce a peak torque of
up to 100 Nm. This high torque has the potential to damage the steering system
or the gearbox which is only rated for peak torques of 30 Nm. Because of this it
must be ensured that the wheel is never driven right up till the end of its
travel to prevent the motor stalling against the end and generating these
forces. The encoder must be calibrated upon each setup of the system. This is
because the encoder only outputs change in rotation and the rack may be in any
position when the system is initialised. Because of this limit switches will be
placed on small plates attached to the rack shaft to indicate when it has
reached the end of its travel. On start up the motor will locate both limit
switches to calibrate its location. These limit switches will also act as kill
switches during operation to prevent the motor reaching the end of its travel.

\section{Controlling the motor and actuator}

Both systems operate on 24V. This was done as the go-kart already had a 24V rail
for driving the main motor. Using the same voltage saves money and simplifies
the design as it precludes the need for converters that would have to be capable
of the 12A peak currents produced by the system. Both systems are controlled
through an H-Bridge interfaced with a SAM7 processor connected to a can bus.
These SAM7s take care of all the low level control required to operate the
drives allowing the main control computer to operate them at a high level with
instructions that corresponds to desired behaviour rather low level drive
operation.

The SAM7 responsible for steering will take the desired wheel angle as an input
from the can bus. It will also track the encoder's output to calculate the
turning angle. Running a PID controller between the setpoint and current value
it will send the PID loops output as a PWM signal to the H-bridge.

The design of the linear actuator is similar. The SAM7 will be passed the
current and desired speeds of the go-kart. From this and the voltage output by
the potentiometer built into the linear actuator the error in the actuator's
location will be found. Again a PID controller will drive a PWM signal to the
H-bridge controlling the actuator.

\section{High-level logic and control}

For high level control it was decided to design a system where the go-kart can
be fully controlled by a laptop using a simple USB interface.  There are a few
reasons behind this decision, the biggest one would have to be the much nicer
programming environment presented on a standard PC.  A large availability of
higher level languages and better libraries for any low level stuff that may be
required means that it will be easier to design and build the control system.

This also makes it much simpler to interface to a set of more complex sensors,
doing any sort of computer vision system on an embedded system would require a
lot more effort to design, build and test than doing the same on a standard PC.

To support this simple USB interface a modular design will be employed, a
general overview of the approach can be seen in Fig. \ref{can-design}.

\begin{figure}
  \centering
  
  \caption{Basic go-kart control system overview.\label{can-design}}
\end{figure}

\subsection{CAN bus}

The first decision required for the design of the logic boards was what
communication protocol should be used between boards, it would require only a
low data rate but it would have to be able to communicate over at least 3 meters
and be resistant to noise.  Because the go-kart is driven by a large electric DC
motor, there is likely to be electromagnetic noise in the vicinity of the
go-kart.

Our first thoughts on this was the simple serial buses that we had used
previously; Universal Asynchronous Receiver/Transmitter (UART), Serial
Peripheral Interface bus (SPI) and Inter-Integrated Circuit
(I\textsuperscript{2}C).  Unfortunately these buses are limited in range and can
be highly susceptible to noise.

Dr. Michael Hayes (personal correspondence, April 2011) suggested
Controller-Area Network (CAN-bus) or Local Interconnect Network (LIN-bus) as
industry standard bus-systems used in automotive applications.  Because of their
design they are very robust standards that will work well in a high noise
environment.

CAN-bus utilises a high level message-based, multi-master protocol with
automatic priority based arbitration-free transmission.  The original
specification defined up to the transfer layer (link layer in the OSI standard
model), which takes care of tasks such as fault confinement, error detection,
message validation, acknowledgement, arbitration, message framing, transfer rate
and timing and information routing.  The ISO 11898-2 standard defines high-speed
MAC and physical layers to allow a full implementation of the bus.  This
standard utilises a two-wire balanced signalling scheme which allows for high
common noise rejection and is capable of up to 1 Mbit/s transmission rates, far
more than we will be requiring.

LIN-bus is a small, slow network system that is commonly used as a cheap
sub-network of a CAN bus.  It utilises a master-slave architecture without
collision detection and supports up to 16 slaves.  The communications happen
over a single wire capable of up to 19.2 kbit/s with a 40 meter bus.  Again this
would be enough for our limited communications need, and as we only need 5 nodes
the 16 slave limitation doesn't matter.

After careful consideration of the advantages and disadvantages of all the above
buses the CAN-bus was chosen as the bus to use. 

\subsection{SAM7X}
To control the various parts of the go-kart we have decided to use the
AT91SAM7X256\cite{SAM7Xdatasheet} manufactured by Atmel. This MCU is
based on the ARM7 architecture with 256 kilobytes of flash memory. This chip has
been in previous University of Canterbury assignment and can be purchased from
both Digikey and Element 14.

To implement the CAN bus we needed to use a MCU that supported a hardware based
CAN bus controller. The other choices of MCUs to use, that provided this
functionality, are the ATmega64C1 or AT90CAN. We chose the SAM7X over these two
options mostly because we wanted to stick with a familiar architecture. The
other large consideration that influenced our decision was that we wanted a MCU
that provided a built in USB device port. 

\section{Simple autonomous behaviour}

Currently we plan to develop a simple program that will allow the kart to autonomously follow a person or other vehicle. This system was chosen as it can be quickly implemented, acts as a demonstration of how the system will operate and can provide a useful real world application. This program would allow the go-kart to operate as a smart trolley allowing a person to transport equipment between two locations. While at first glance this program may seem to have limited real world applications a robot known as ``big dog'' is currently being developed to perform the same function carrying 100kg of equipment over rough terrain\cite{bigdog}.

A decision as to how the marker will be tracked is still to be made, however it has been narrowed down to one of two options. The first option is to use the marker as a ball of known shape size and color and have this tracked by a webcam. This system would be cheap and easy to implement but inaccurate and error prone with the ball always having to be clearly visible.

The second option is to use a marker that sends out pulses that are picked up by three RF receivers. This option while more difficult and will take longer to get working would be far more robust and accurate offering superior performance.

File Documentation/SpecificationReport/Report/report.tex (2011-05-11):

% PREAMBLE
\documentclass[a4paper, 12pt, titlepage, openany]{book}
\usepackage[top=1in,right=2.5cm,left=2.5cm,bottom=1in]{geometry}
\usepackage{mathptm}
\usepackage{hyperref}
\usepackage{epsfig} 
%\usepackage{tipa}
% Commented out so that the build will work on the cosc server - wgl18 20110506
\usepackage{subfigure}
\usepackage{footnote}
\usepackage[gnu]{newtitle} 
\usepackage{fancyheadings} 
\usepackage[numbers,square]{natbib}
\pagestyle{empty}
\usepackage[grey,times]{honoursThesis}
\usepackage{listings}
\usepackage{multirow}

\setlength{\parindent}{0in}
\setlength{\parskip}{0.15in}

% TITLE PAGE
\title{Anonymous Go-Kart: Specification Report}
\date{\today}

% Project Title, Supervisor, Student Name (s) and ID and Emails
\author{
  {Henry Jenkins}\vspace{-0.1cm}\\
  {\tt hvj10@uclive.ac.nz (83238549)}\vspace{0.2cm}\\
  {Wim Looman}\vspace{-0.1cm}\\
  {\tt wgl18@uclive.ac.nz (92692734)}\vspace{0.2cm}\\
  {Simon Richards}\vspace{-0.1cm}\\
  {\tt scr52@uclive.ac.nz (84974076)}\vspace{0.2cm}\\
  {Zachary Taylor}\vspace{-0.1cm}\\
  {\tt zjt14@uclive.ac.nz (76691819)}\vspace{1.0cm}\\
  {\LARGE Supervisor}\vspace{0.3cm}\\
  {Dr Andrew Bainbridge-Smith}\vspace{-0.1cm}\\
  {\tt andrew.bainbridge-smith@canterbury.ac.nz}\vspace{1.0cm}\\
    Department of Computer and Electrical Engineering\vspace{0.1cm}\\
    University of Canterbury, Christchurch, New Zealand}
\setcounter{tocdepth}{1}
\begin{document}

\maketitle
% I removed the next line to remove blank page after title page - Henry
\pagenumbering{roman}
\frontmatter
\thispagestyle{empty}
\input{Abstract}

\pagestyle{fancy}

\renewcommand{\chaptermark}[1]
{\markboth{\uppercase{\thechapter.\ #1}}{}}
%\renewcommand{\sectionmark}[1]
%{\markboth{\uppercase{\thesection.\ #1}}{}} % Changed so the section is on both. - Wim
\setlength{\headrulewidth}{0.5pt} \setlength{\footrulewidth}{0pt}

\newcommand{\helv}{\fontfamily{pag}\fontseries{b}\fontsize{9}{11}\selectfont}

% Changed these so page numbers are always on the right and the headers are
% always on the left. - Wim
\lhead[\helv \leftmark]{\helv \leftmark}
\rhead[\helv \thepage]{\helv \thepage}
\cfoot[]{}

\newpage
\tableofcontents
\newpage

\mainmatter
    \input{ProjectOverview}
    \input{Requirements}
    \input{Approach}
    \input{Budget}
    \input{Conclusion}
    \newpage

\newpage
\bibliographystyle{plainnat}
\bibliography{report}
%\addcontentsline{toc}{chapter}{Bibliography}

\appendix
    \input{Appendix}
    
\end{document}

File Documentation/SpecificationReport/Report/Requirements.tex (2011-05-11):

\chapter{Requirements}
\section{Goals}
Given the continuous nature of this project the only constraint upon our progress is time. The issue here is that we may set goals beyond what we have time to achieve, and consequently fail those goals.

To avoid doing this we have split the project's measurable goals into two categories, those we need to achieve to at least deliver a platform for future groups (i.e. implementing drive-by-wire); and those we need to run the go-kart at a behavioural level. As the goals in the second category require the completion of those in the first, they have a lower priority for us. We expect to achieve drive-by-wire control within the deadline, however completing the behavioural control aspect may not be a realistic goal due to the time constraints.

\subsection{We Expect to Achieve}
A fully Drive-by-Wire go-kart controllable over a USB link. Safety constraints, an interface for sensors and low level control of braking, steering and motor power that will all be provided by an embedded system. If this is all completed without any progress on the behavioural software then the USB command interface will need to be documented for future groups.

\subsection{We Hope to Achieve}
The abstraction of the control of the kart's systems (steering wheel angle, brake force etc.) into higher level commands such as speed and direction. The selection and integration of an array of sensors onto the go-kart allowing sufficient information for autonomous control.

An example application proving the go-kart's `autonomous-ness'. This will require a software application running on a laptop, and the sensors connected to the laptop through a micro-controllers. We had originally hoped that this application would demonstrate object detection and avoidance however due to time constraints this application will most likely be of a more basic nature that shows off the potential of the system rather then being a solution that demonstrates what autonomous systems are capable of.

\section{Specifics}
Each set of goals mentioned above covers one of the two components we have split the project into. They are the drive-by-wire (DbW) system and the PC-based behavioural control. The specific requirements of each subsystem are defined below.

\subsection{Drive-By-Wire}
In order to achieve full computer control all of the go-kart's mechanical control systems must be replaced with electromechanical actuators interfaced through a micro-controller network. Additionally, the same network must control the go-kart's electric motor and gather feedback from all systems for full, closed-loop control.

Since the go-kart has an electric motor there are two components requiring actuation, the brake and the steering mechanism.

\subsubsection{Braking}
The braking system requires linear actuation to drive the hydraulic  brake. 

\subsubsection{Steering}
The existing steering system uses a rack and pinion system to steer. Converting this into a DbW system requires a low speed, high torque motor driving the pinion. The absolute position of of the motor needs to be tracked so the motor can be run in a closed loop.

\subsubsection{Control}
The control system requires a way to set the position of the steering and brake systems using the actuators outlined above. Additional to this is the control of the of the accelerator. This system requires the control system to interface directly to the microcontroller that is running the electric motor.

\subsection{Sensing and Behavioural Control}
An array of sensors must be attached to the kart that provide all the information the go-kart requires to interact with its environment and perform actions without hitting obstacles or requiring human interaction. These sensors must be connected to the main control system. 

To meet what we hope to achieve for this project we must then be able develop a program on a laptop and attach this to the go-kart via a simple to use interface. The program must operate the steering, brakes and accelerator to provide autonomous functions that can be carried out in an uncontrolled environment without human interaction. 

\section{Safety}
Safety is a large concern on this project. The go-kart we are provided with can reach speeds of over 50 kmph and weighs over 100kg. This gives the system the potential to cause serious damage and injuries if we were to lose control. Because of this all stages of design require careful consideration of safetey aspects.

The go-kart will require an on-board kill switch to allow programs to be quickly aborted mid test by a person in the passenger seat. The go-kart's accelerator must be limited to prevent it having the capacity to achieve high speeds. Systems must be implemented to ensure the go-kart stops immediately if any of its controls fail, the laptop battery becomes low or the battery powering the actuators starts to run out of power while the kart is traveling at speed.

The potential for harm caused by the kart is not limited to it hitting objects. The actuators for controlling the kart's mechanical systems will also be applying large amounts of force. This means that the systems will require appropriate guards around their moving parts to prevent fingers or other body parts being caught in the system and injured.

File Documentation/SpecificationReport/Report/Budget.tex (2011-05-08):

\chapter{Budget and Timeline Summary}
% Give a summary of actual and anticipated purchases (include shipping and
% delivery). to met s and results are encouraged, regardless of success. A
% timeline summary from start of the project to completion should be included –
% a Gantt chart may be appropriate.

\section{Budget}
After building preliminary system designs, a bill of materials including parts
costs has been composed. Where possible pieces have been sourced from either Digikey,
Element 14, Mouser or estimated if the components will come from the ECE store.

Currently both the gear motor with encoder and the linear actuator have been
ordered as they have a month lead time coming from the USA. All other components
will be ordered within the next two weeks.

\begin{table}[h]
  \small
  \begin{center}
    %{\scriptsize
    \begin{tabular}{ | l | l | p{.40\textwidth} | l | l | l | l | }
      \hline
      & Part Number & Description & Qty & Cost & Subtotal \\
      \hline
      Steering & IG52 – 04 & 24VDC 10rpm Gear Motor with Encoder & 1 & \$185.00 & \$185.00 \\
      & Shipping & Gear Motor Shipping & 1 & \$75.00 & \$75.00 \\
      & DRV8432 & Motor Driver & 1 & \$16.00 & \$16.00 \\
      &  & Mounting Bracket & 1 & \$50.00 & \$50.00 \\
      \hline
      Braking & 5 1752 & 4\texttt{"} stroke 100lb 24VDC Linear actuator  & 1 & \$50.00 & \$50.00 \\
      & Shipping & Linear actuator Shipping & 1 & \$50.00 & \$50.00 \\
      &  & Mounting Bracket & 1 & \$50.00 & \$50.00 \\
      \hline
      Accelerator & ATMEGA8L & Interface to go-kart power control & 1 & \$5.16 & \$5.16 \\
      & LM317KCS & IC VOLT REG POS ADJ & 1 & \$1.13 & \$1.13 \\
      &  & PCB & 1 & \$20.00 & \$20.00 \\
      \hline
      CAN Bus & PL-STP6-0 & 0.5M Cat6 STP Lead (CAN Bus) & 3 & \$4.50 & \$13.50 \\
      & PL-STP6-1 & 1.0M Cat6 STP Lead (CAN Bus) & 1 & \$5.70 & \$5.70 \\
      & SS60000-009G & RJ45 JACK (CAN Input/output) & 10 & \$4.96 & \$49.60 \\
      & Header 10X2 & Header, 10-Pin, Dual row (JTAG ) & 5 & \$1.00 & \$5.00 \\
      & fdd8445 & MOSFET 40V, 50A, 8.7mΩ & 5 & \$2.00 & \$10.00 \\
      & SW-PB & Switch (Reset) & 5 & \$3.00 & \$15.00 \\
      & AT91SAM7X & Microcontroller (CAN Controller) & 5 & \$19.37 & \$96.85 \\
      & ATA6660 & High Speed CAN Transceiver & 5 & \$2.47 & \$12.35 \\
      & AE9925-ND & USB Type B connector & 5 & \$1.52 & \$7.60 \\
      & MCP130T-300I & Microcontroller Supervisory Circuit & 5 & \$0.76 & \$3.80 \\
      &  & PCB Manufacture and shipping & 1 & \$217.00 & \$217.00 \\
      \hline
      Other &  & Misc Components (Diodes, Resistors, Capacitors, Wire, Headers) & 1 & \$60.00 & \$60.00 \\
      & Shipping & Shipping from Digikey and Element14 & 1 & \$30.00 & \$30.00 \\
      \hline
      &  &  &  & Total & \$1,030.69 \\
      \hline
    \end{tabular}
  \end{center}
  \caption{Bill of Materials for Autonomous Go-Kart}
\end{table}

\section{Timeline}
The Autonomous Go-Kart project has been broken down into small sections then
time allocations have been put next to each task. Where possible we have put in
dependencies between each of the tasks. However this model of only starting one
task once the previous one has been completed is not very accurate. For example
the control software has been represented as requiring the hardware to be
complete. Actually the control software will be started much before the hardware
is complete.

To make sure the project deadlines are met, milestones have been added for each
assessment or deliverable. This puts the whole year in perspective, including
where we are currently with handing in the specification report. There will also
be weekly milestones added that will be set and evaluated each meeting. These
weekly milestones are to ensure we keep on track with the scheduled timeline.

  \begin{figure}[h]
    \centering
    %\includegraphics[width=0.5\textwidth]{Images/TB9100.jpg}
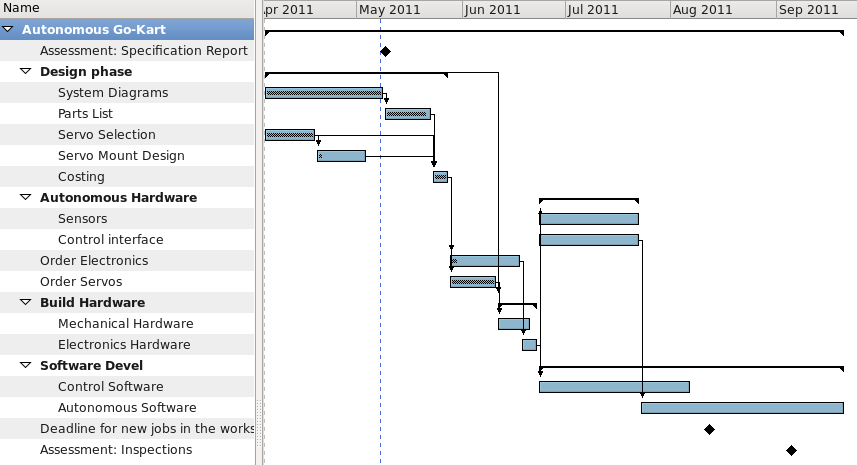
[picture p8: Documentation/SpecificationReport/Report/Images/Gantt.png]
    
    \caption{Gantt chart of the Autonomous Go-Kart project}
    \label{gantt_chart}
  \end{figure}

Currently the timeline of the project extends past the inspection milestone.
After working out how long each task would take we noticed that the sub project
tasks included in Sensing and Behavioural Control are very likely to push the
project time past the inspection deadline. This means that currently the chances
of achieving all of our goals are slim. However assuming we are able to stick to 
this plan, we expect to achieve our goal of Drive-by-Wire control within the given
time frame.

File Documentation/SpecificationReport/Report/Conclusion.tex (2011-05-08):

\chapter{Project Risks and Conclusions}

The project was divided up into several modules as was outlined in the approach and preliminary design section. The current status and discussions of our ability to complete these modules are outlined below.

\begin{description}
\item[Drive by wire] For this system we have already completed a fairly detailed preliminary design on how the system will work, how the different sections will communicate and begun ordering the required parts. We are all fairly confident that we will have this section completed well within the allotted time for the project

\item[Sensor interfacing] While there are no concrete plans for this module as of right now the group has began to research which sensors would best suit the application and are within our budget. The group has also looked into the best way to interface them with the control system. Again we are fairly confident that this section can be completed in the time allowed

\item[High level control of systems] For this section we do not yet have detailed plans for functions required however we have brainstormed what many of them will be and what sensors they will require. We believe that as long as no unforeseen problems occur during earlier parts that this is again achievable.

\item[Simple autonomous behaviour] Apart from the idea of what we wish the kart to do and a rough idea of some of the programming that would be involved no work has been done on this section. We currently believe that if all other sections are problem free and go smoothly that we may have time to finish a mostly functional version of this behaviour. We do not, however, feel we will have time to get this system working 100\%.

\item[Complex autonomous behaviour] We believe that getting the vehicle to a point where this part is operational is a pipe dream. It is our goal this year to develop the system to the point where groups in future years will be able to start at this point allowing them more time to develop the highly complex algorithms this step requires. If time allows we will begin on this section however currently this appears unlikely.
\end{description}

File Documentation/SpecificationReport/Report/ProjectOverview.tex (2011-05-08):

\chapter{Project Overview}

The aim of this project is to convert an existing electrically powered go-kart into an autonomous vehicle with the ultimate goal of circumnavigating a campus building without human interaction.

Autonomous vehicles and more specifically driverless cars are part of a field of research that has seen a large amount of development in the last few years. This research comes as the increasing power of computers makes the processing of sensors and the decision making required by these vehicles able to happen in real time even when the vehicle is travelling at high speeds.

There are many advantages to this automation. These include improved safety (annual road deaths currently stand at 1.3 million\cite{WHO}) by preventing road accidents caused by human error, the transportation of loads in dangerous areas such as disaster zones and improving traffic flow. For these advantages to be realized however robust programs must be developed that will allow the vehicle to adapt to operate in a varied and continually changing environment with many unknown variables to compensate for.

Recent projects in this area can be divided into two main areas. Vehicles for surfaced roads and free ranging vehicles. On surfaced roads the major current project is the Google driverless car \cite{google_car_blog}. This system combines information gathered by Google street view with information from its on board sensor array to drive on highways with no human interaction. To date these vehicles have driven over 200,000 km without any incidents. A second major driverless vehicle project was the VisLab Intercontinental Autonomous Challenge which ran in 2010. In this challenge 4 autonomous vehicles were driven on a 15,000 km trip from Parma, Italy to Shanghai, China with almost no human interaction \cite{vislab}.

 In free ranging vehicles the DARPA grand challenge run by the US military offered contestants a \$2 million prize for the autonomous vehicle that could complete their off road coarse in the shortest time. The winner of this race vehicle in 2007 completed the 96km course in 4 hours 10 minutes averaging 23 km/h over rough terrain \cite{darpa}.

All recent large projects into autonomous vehicles have made extensive use of LIDAR (light detection and ranging) sensor that rapidly scans a laser over the environment measuring distances to create a map of the surroundings. These maps can then be used to allow the program to make decisions about its operation based on a very accurate picture of the world. The only disadvantage with the LIDAR is its large price tag when compared to any other form of sensors. A low cost LIDAR that can operate in direct sunlight costs in excess of \$5000.

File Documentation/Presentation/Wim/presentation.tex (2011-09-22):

\documentclass[xcolor=dvipsnames]{beamer}
\useoutertheme{infolines} 
\usetheme[height=7mm]{Rochester} 
\usefonttheme{structuresmallcapsserif}
\setbeamertemplate{items}[ball] 
\setbeamertemplate{blocks}[rounded][shadow=true] 
\setbeamertemplate{navigation symbols}{} 
\usepackage{tikz}
\usepackage{ellipsis}

\definecolor{mygreen}{RGB}{127, 159, 127}
\definecolor{myyellow}{RGB}{224, 207, 159}
\definecolor{fgColor}{RGB}{220, 220, 204}
\definecolor{bgColor}{RGB}{63, 63, 63}
\setbeamercolor{normal text}{bg=bgColor, fg=fgColor}
\setbeamercolor{structure}{fg=mygreen}
\setbeamercolor{palette primary}{fg=bgColor}
\setbeamercolor{palette secondary}{bg=structure.fg!90!black, fg=bgColor}
\setbeamercolor{palette tertiary}{bg=structure.fg!80!black, fg=bgColor}
\setbeamercolor{item projected}{fg=bgColor}
%\setbeamercolor{block title}{fg=bgColor,bg=myyellow}

% Use symbols for footnotes.
% 1 - *
% 2 - dagger
% 3 - double dagger
\renewcommand{\thefootnote}{\fnsymbol{footnote}}

\author{ Wim Looman\footnotemark[2] }
\title{Software Engineering}
\subtitle{In the Mariokart system}
\institute[UC]
{
  Department of Electrical Engineering\\
  University of Canterbury\\
  Christchurch\\
  New Zealand
}
\date{26 September, 2011}

\begin{document}
  \begin{frame}[plain]
    \titlepage
    \footnotetext[2]{\href{mailto:wgl18@uclive.ac.nz}{\texttt{wgl18@uclive.ac.nz}}}
  \end{frame}

  \begin{frame}{Outline}
    \begin{center}
      \begin{minipage}{0.5\linewidth}
        \tableofcontents
      \end{minipage}
    \end{center}
  \end{frame}

  \section{Build Toolchain}
  \subsection{GNU, GNU, GNU}
    \begin{frame}{Build Toolchain}
      \Large
      \begin{itemize}
        \pause \item \texttt{arm-eabi-gcc} -- The GNU Compiler Collection
        \pause \item \texttt{arm-eabi-gdb} -- The GNU Project Debugger
        \pause \item \texttt{openocd} -- Open On-Chip Debugger
        \pause \item GNU \texttt{make}
        \begin{itemize}
          \item Lots of targets to enable easy programming, debugging and testing.
        \end{itemize}
      \end{itemize}
    \end{frame}

  \section{Source Control}
    \subsection{Git}
      \begin{frame}{Git}
        \Large
        \begin{itemize}
          \pause \item Distributed Version Control System (DVCS)
          \pause \item Created by Linus Torvalds for the Linux kernel project.
          \pause \item High performance and strong safeguards against corruption.
          \pause \item Very \emph{``branch-friendly.''}
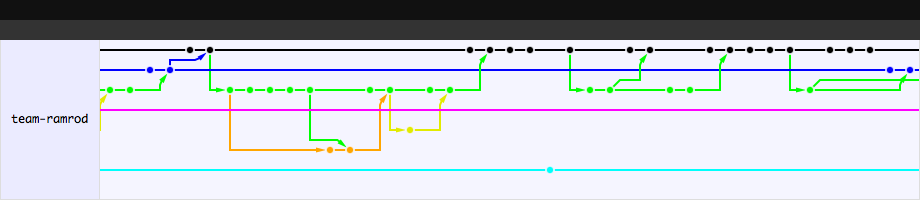
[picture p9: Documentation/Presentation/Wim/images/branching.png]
                       
        \end{itemize}

      \end{frame}

    \subsection{Github}
      \begin{frame}{Github}
        \only<1>{
          \begin{block}{About}

            \emph{``Originally founded by Chris Wanstrath, PJ Hyett and Tom
            Preston-Werner as a project to simplify sharing code, GitHub has
            grown into an application used by nearly a million people to store
            over two million code repositories, making GitHub the largest code
            host in the world.''}~--~\url{https://github.com/about}

          \end{block}

        }
        \only<2>{
          \Huge \centering \scshape{Web Interface}\footnotemark[2]

          \vspace{0.5\baselineskip}
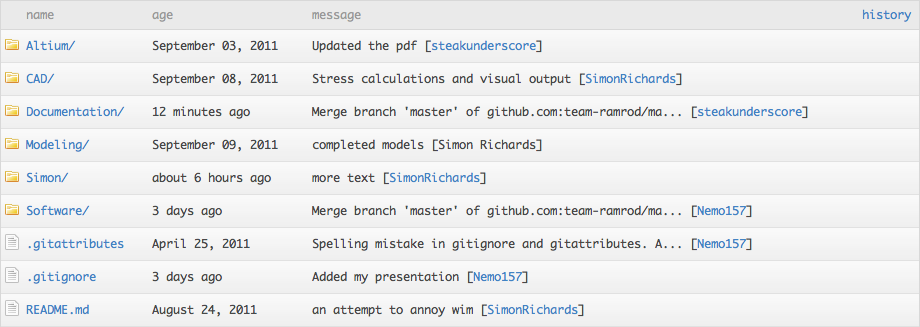
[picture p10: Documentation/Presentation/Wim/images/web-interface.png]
          

          \footnotetext[2]{\url{https://github.com/team-ramrod/mariokart}}
        }
        \only<3>{
          \Huge \centering \scshape{Wiki}\footnotemark[2]

          \vspace{0.5\baselineskip}
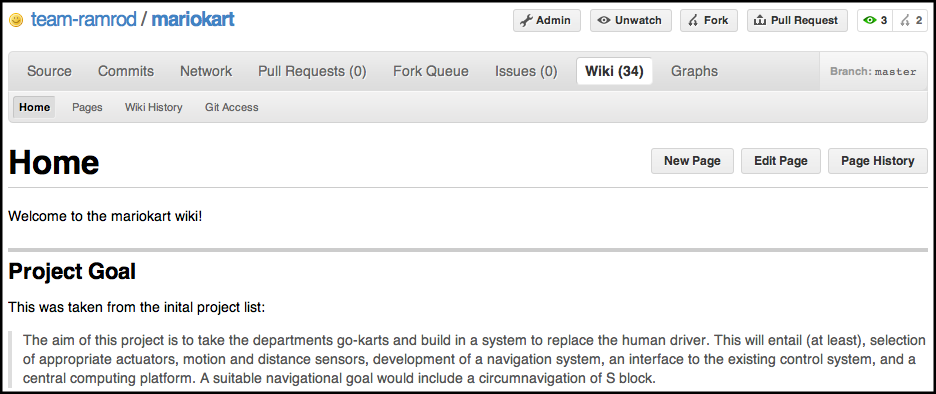
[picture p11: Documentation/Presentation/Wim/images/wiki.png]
          

          \footnotetext[2]{\url{https://github.com/team-ramrod/mariokart/wiki}}
        }
      \end{frame}

  \section{Continuous Integration}
    \subsection{What is it?}
      \begin{frame}{What Is Continuous Integration?}
        \begin{center}\begin{minipage}{0.8\linewidth}\begin{block}{Definition\footnotemark[2]}

              \emph{``Continuous Integration is a software development
              practice~\dots\ leading to multiple integrations per day~\dots\
              verified by an automated build~\dots\ to detect integration errors
              as quickly as possible.''}~---~Martin Fowler

        \end{block}\end{minipage}\end{center}

        \footnotetext[2]{\url{http://martinfowler.com/articles/continuousIntegration.html}}
      \end{frame}

    \subsection{Why would you use it?}
      \begin{frame}{Why Would You Use Continuous Integration?}
        \Large
        \begin{itemize}
          \pause\item Detect errors early.
          \vspace{\baselineskip}
          \pause\item Minimizes time between error introduction and fix.
          \vspace{\baselineskip}
          \pause\item Provides a stable base for future work.
          \begin{itemize}
            \pause \item \large Very useful for branch-happy development in git.
          \end{itemize}
          \vspace{0.5\baselineskip}
          \pause\item Peer pressure.
        \end{itemize}
      \end{frame}

    \subsection{CI Joe}
      \begin{frame}{CI Joe\footnotemark[2]}
        \only<1>{
          \begin{center}\begin{minipage}{0.65\linewidth}\begin{block}{Repository Description}
            \emph{``CI Joe is a fun Continuous Integration server.''}
          \end{block}\end{minipage}\end{center}
        }

        \only<2->{
          \begin{itemize}
            \Large
            \item<2-> Simple setup.
            \vspace{\baselineskip}
            \item<3-> Designed to work with git.
            \vspace{\baselineskip}
            \item<4-> Can trigger a build via a post-hook on github.
            \vspace{\baselineskip}
            \item<5-> Reports status via build-hook (used to send email).
          \end{itemize}
        }

        \footnotetext[2]{\url{https://github.com/defunkt/cijoe}}
      \end{frame}

    \subsection{Examples}
      \begin{frame}{Example 1}
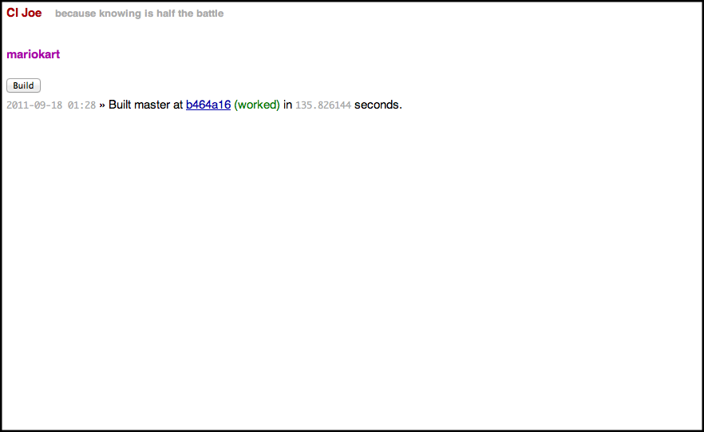
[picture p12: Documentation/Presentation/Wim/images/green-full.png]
        \only<1>{\vspace{9px}}
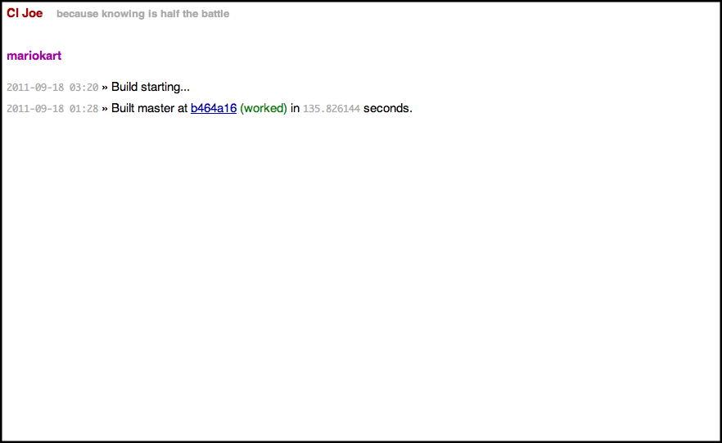
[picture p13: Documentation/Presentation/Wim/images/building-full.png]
        \only<2>{}
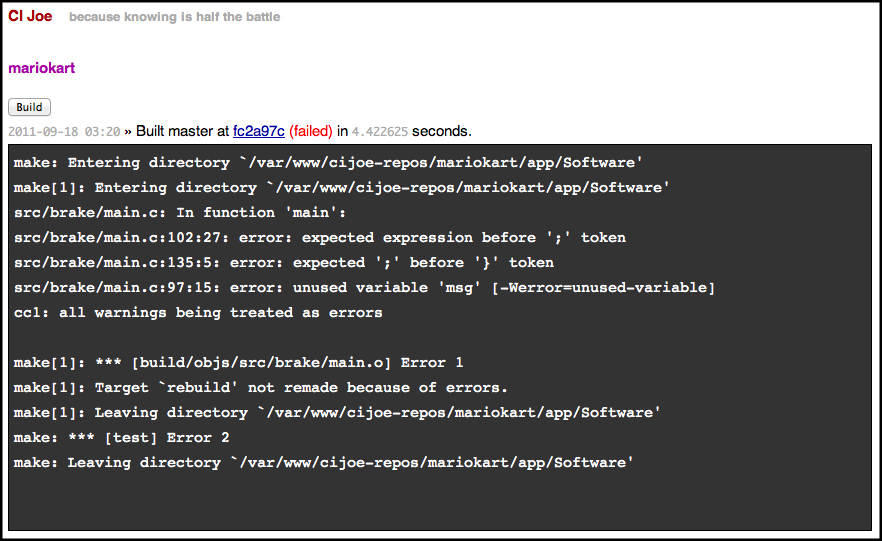
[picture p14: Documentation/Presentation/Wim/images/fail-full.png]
        \only<3>{}
      \end{frame}

      \begin{frame}{Example 2}
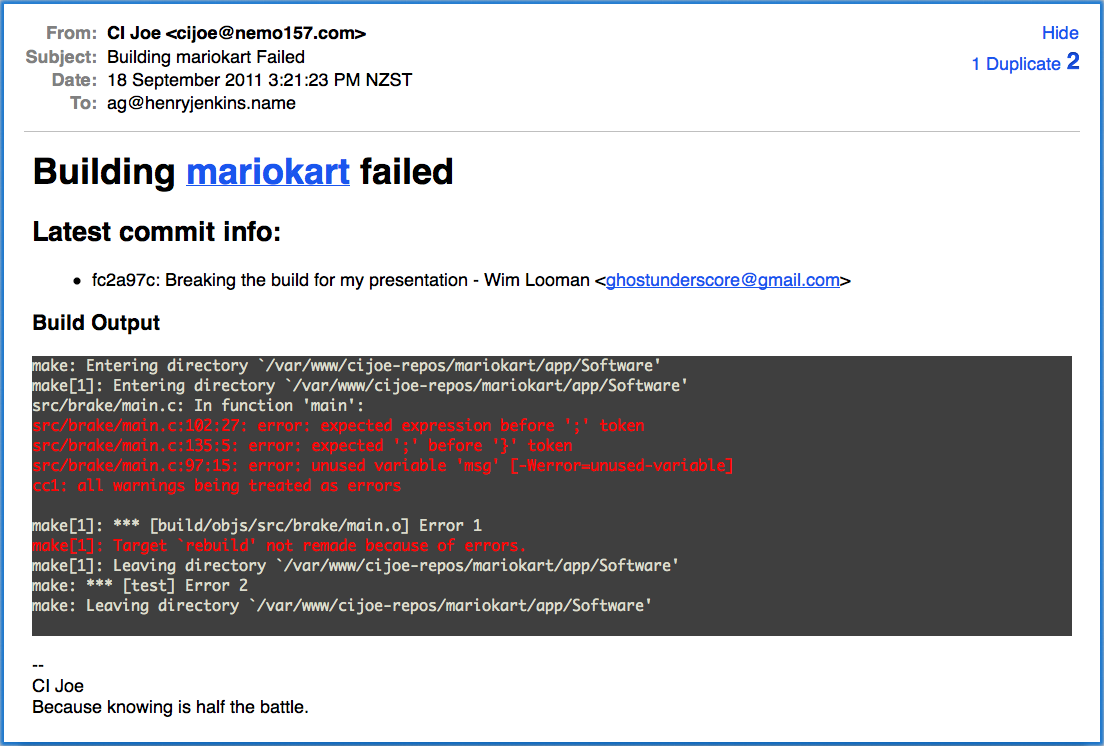
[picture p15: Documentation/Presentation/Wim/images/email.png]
        
      \end{frame}

    \section{Questions}
      \begin{frame}[plain]
        \begin{tikzpicture}[remember picture,overlay]
          \node[at=(current page.center)] {
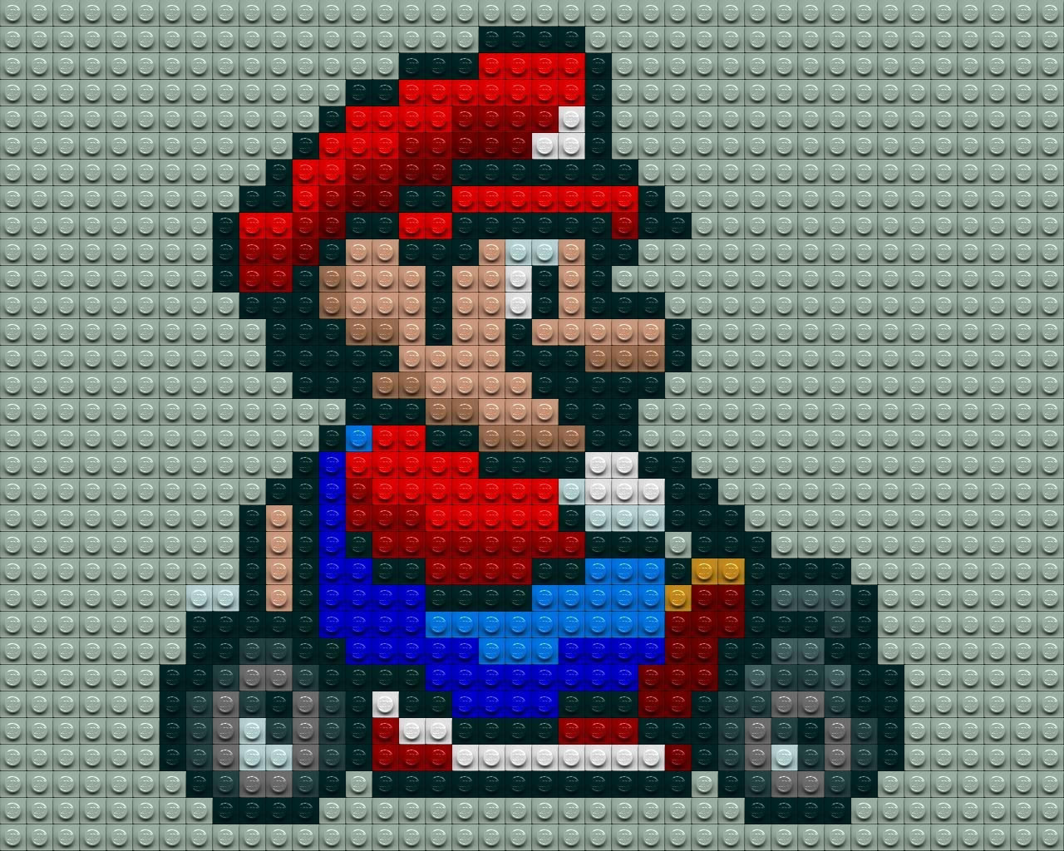
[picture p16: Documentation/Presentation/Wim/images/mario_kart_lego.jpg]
            
          };
        \end{tikzpicture}
      \end{frame}

    \begin{frame}{Git vs SVN}
      \begin{columns}
        \column{0.45\textwidth}
          \begin{block}{Git}
            \begin{itemize}
              \item Distributed (central repository can be used).
              \vspace{0.5\baselineskip}
              \item Every clone is a full repository.
              \vspace{0.5\baselineskip}
              \item Continual branching and merging is expected.
            \end{itemize}
          \end{block}

        \column{0.45\textwidth}
          \begin{block}{SVN}
            \begin{itemize}
              \item Needs a single central repository.
              \vspace{0.5\baselineskip}
              \item Can't commit without access to central repository.
              \vspace{0.5\baselineskip}
              \item Branching and merging is painful.
            \end{itemize}
          \end{block}
      \end{columns}
    \end{frame}

    \begin{frame}{Unit Testing}
      \begin{itemize}
        \item Initially was planned.
        \vspace{0.5\baselineskip}
        \item Would require mocking and simulating the entire SAM7XC architecture.
        \begin{itemize}
          \item Hundreds to thousands of registers.
          \item Need constraints on which registers get written in which orders.
        \end{itemize}
        \vspace{0.5\baselineskip}
        \item Would be awesome, but probably too large for even its own final year project.
      \end{itemize}
    \end{frame}
\end{document}

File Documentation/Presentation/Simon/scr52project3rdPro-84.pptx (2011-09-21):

## Safety by Design

Designing a distributed system
to mitigate and eliminate risk

## Overview

- Many sources of risk in a project like this one.
- Inherited problems - Not our concern.
- Hardware problems - easy to test for.
- Software problems – Some easy some hard.

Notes: Easy to test for the bugs that present themselves often. Errors that take some time or certain conditions to manifest themselves are not likely to be discovered during testing.
The first set of problems we can discover and correct in the testing phase. For issues we cannot solve we can set guidelines to mitigate problems: Speed limiting, kill button, checking connections etc.

## Modelling

- What is a model.
- What does a model not do: implementation and calculation
- What's the point?
SPIN/Promela:
SPIN, the Simple Promela INterpretor, is a tool used to simulate and verify the correctness of models described in the Promela language.

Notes: The motivation to model a software system is the same as modeling a physical system. Two things: developing software takes resources and so a simple model can lead the design down an already proven path; faulty software has the same capacity to cause harm as a poorly designed bridge.

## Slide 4

Modelling Mariokart

The implementation has a master board plus four slave boards.
All boards connected to the CAN bus.
All boards follow the same state machine.
It is important that all boards are in a consistent state.

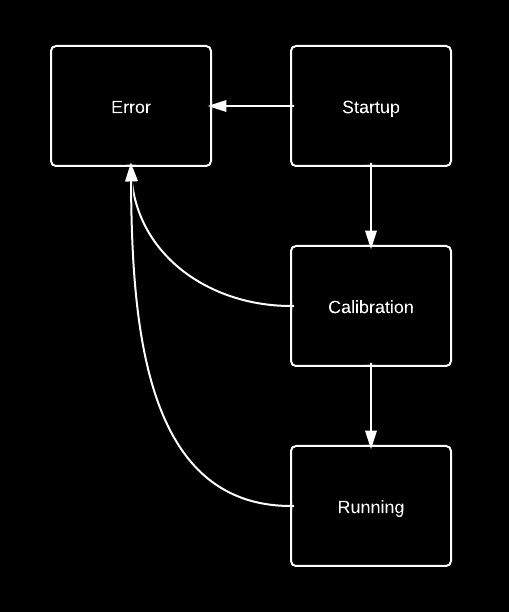
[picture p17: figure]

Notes: Briefly describe CAN bus, its uses and strengths.

Hence global state is the set of all boards’ current state.
The reasons and outputs of the states shown isn’t really relevant
Consistent state – inconsistent states must last for a negligible time

## Modelling Mariokart

- The master board drives all state transitions.
- Except: all boards can drive an error state transition.
- All boards may non-deterministically reset or discover an error at any point.
- Correctness claims. System either executes running cycle infinitely or all boards transistion to error state.

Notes: All boards may non-deterministically reset or discover an error (for example an actuator is jammed) at any point. SPIN will evaluate all possible executions.

## Conclusions

- Model verification finds particular class of error while modelling acts as a design tool.
- Worthwhile for systems where the consequences of design errors are high.
- Result: an already proven design was implemented with confidence.

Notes: Modeling finds issues caused by bad software design.
Worthwhile due to high risk (e.g. Shuttle controls) or high usage.

Analogise modelling to sketching (but for software)

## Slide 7

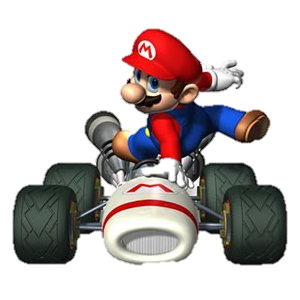
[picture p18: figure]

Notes: Obligatory plumber picture

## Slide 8

/**
* A simplified version of the
* client board model.
*/
proctype Client(chan input) {
Startup:
input?message
comms!message
Calibration:
// calibration stuff
Running:
do
:: // Normal loop
:: // Restart board
:: goto Error
od;
Error:
broadcast!error;
}
/**
* If one board goes into error state,
* they all must (eventually).
*/
never {
do
:: error_count > 0 -> break
:: true -> skip
od;
accept:
do
:: error_count != 3
od;
}

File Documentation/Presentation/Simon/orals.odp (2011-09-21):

## Safety by Design

  Designing a distributed system
  to mitigate and eliminate risk

## Overview

- Many sources of risk in a project like this one.
- Inherited problems - Not our concern
- Hardware problems - easy to test for.
- Software problems – Some easy some hard,
  Easy to test for the bugs that present themselves often. Errors that take some time or certain conditions to manifest themselves are not likely to be discovered during testing.
  The first set of problems we can discover and correct in the testing phase. For issues we cannot solve we can set guidelines to mitigate problems: Speed limiting, kill button, checking connections etc.

## Modelling

- What is a model.
- What does a model not do: implementation, calculation
- What's the point.
  SPIN/Promela
- SPIN, the Simple Promela INterpretor, is an tool used to simulate and verify the correctness of models written in the Promela language.

## Modelling Mariokart

- The implementation has a master board plus four slave boards.
- The master board drives all state transitions.
- All boards can drive an error state transition.
- All boards may non-deterministically reset or discover an error (for example an actuator is jammed).
- Correctness claims

## Conclusions

- Model verification finds particular class of error.
- Worthwhile for systems where the consequences of
  design errors are high.

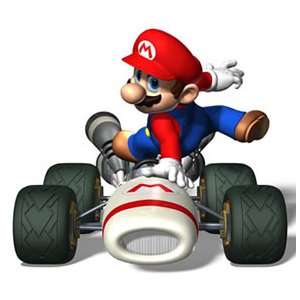
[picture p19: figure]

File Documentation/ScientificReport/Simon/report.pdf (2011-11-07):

# Safety by Design for the Mariokart System

### Simon Richards

scr52@uclive.ac.nz

### Coauthors: Wim Looman, Zachary Taylor Henry Jenkins and Dr Andrew Bainbridge-Smith

wgl18@uclive.ac.nz zjt14@uclive.ac.nz hvj10@uclive.ac.nz andrew.bainbridge-smith@canterbury.ac.nz

Department of Electrical and Computer Engineering University of Canterbury
Christchurch, New Zealand

Abstract—An electric go-kart is outfitted with a driveby-wire system in the first phase of development of an autonomous vehicle. The safety aspects of the design are evaluated and analysed using typical project management techniques. A model of the distributed software required is developed and proven and the place of modelling in software engineering is discussed..

I. INTRODUCTION
A. Project Description
The authors’ reports are based on a group project carried out in the final year of their Bachelor of Engineering degree at Canterbury University. The original goal of this project was to take one of the electric go-karts used by the department for power electronics projects and convert it into an autonomous vehicle capable of a simple navigation task. Due to time restrictions the aim was reduced to implementing the mechanical and electronic systems needed to control the kart’s motion over a USB link.
The authors refer to the project using the moniker Mariokart and this name may be used throughout this report in reference to the team, the vehicle or the project itself.
B. System Design
The overall system design consisted of a laptop, electronics, a CAN bus, actuators and an interface to the existing motor driver hardware.
- Electronics: Five PCBs were located around the kart, each in close proximity to the sub-system it was responsible for. The PCBs were identical in layout, specialisation was achieved by removing components from boards where they were not needed. For example it was intended for only one board to communicate directly with a laptop and so the other boards did not have USB headers. The decision to distribute control was made primarily to avoid problems caused by driving motors and actuators over a long distance in a high noise environment.
- Actuators: The brake pads were driven by a linear actuator mounted in place of the brake pedal. The actuator was mounted to the floor of the go-kart and its driver board was situated nearby. The steering column was similarly controlled by a DC motor mounted in place of the steering wheel and fixed to the frame. The DC motor included an encoder so that the relative angle of the steering column could be determined. Limit switches at each extreme of rotation ensures the motor does not turn too far and allows for the absolute angle to be measured.
- Controller laptop: To simplify use for future projects, the entire system is controllable via commands sent over a USB cable. The communications board is responsible for interfacing with a laptop and distributing the user’s commands
- Motor interface: Power electronics and a motor driver had already been implemented as part of a student project so the only requirement from the motor driver board was to interface with this over the available SPI link.
- The CAN bus: CAN is a multi-master serial bus with guaranteed sending and message priority. It was designed by Robert Bosch GmBH for networking micro-controllers in automobiles and has also some popularity in industrial automation. The CAN specification is low-level only, it does not specify a data protocol or a method address allocation. There are numerous similar software stacks built on top of CAN for various purposes such as the Society of Automotive Engineers’ J1939 [1] however due to the simplistic nature of our network we implemented our own protocol.
For a more detailed description and justifications see Embedded Hardware Design For Autonomous Electric Vehicle [2].
C. Risk

As with any vehicle, autonomous or otherwise, there is always a risk to the user, bystanders and the go-kart itself if a part of the system malfunctions in any way. Replacing a human driver with electromechanical control systems removes the non-deterministic element of human error from the system but adds a new set of risks and potential design mistakes.
In this paper, the sources of these risks will be listed analysed and techniques for mitigation and negation will be investigated and evaluated.

II. SAFETY - A METHOD
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

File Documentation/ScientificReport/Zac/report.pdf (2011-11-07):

# Development of a Marker Following System for use in the Mariokart System

Zachary Taylor
zjt14@uclive.ac.nz

Coauthors: Simon Richards, Wim Looman Henry Jenkins and Dr Andrew Bainbridge-Smith.
scr52@uclive.ac.nz wgl18@uclive.ac.nz hvj10@uclive.ac.nz andrew.bainbridge-smith@canterbury.ac.nz

Department of Electrical and Computer Engineering University of Canterbury
Christchurch, New Zealand

Abstract—An autonomous go-kart system, nicknamed Mariokart was being developed. It required a simple algorithm to demonstrate its abilities and test its systems. To meet this need an algorithm was developed to follow the path of a marker. Three computer vision techniques color detection, SURF and chessboard detection were evaluated to see if they could be used to locate the marker. SURF performed slowly and only at very short ranges, colour detection was found to be too sensitive to lighting changes but otherwise a viable option. Chessboard detection was found to meet all the needs of the system with the exception of having a reasonably short range. Once the method of marker detection was in place a method for allowing the kart to follow the same route as the marker was implemented. This utilized the karts on board sensors to estimate its location. The system was tested but never mounted to the Mariokart due to delays in the development of systems it required to
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

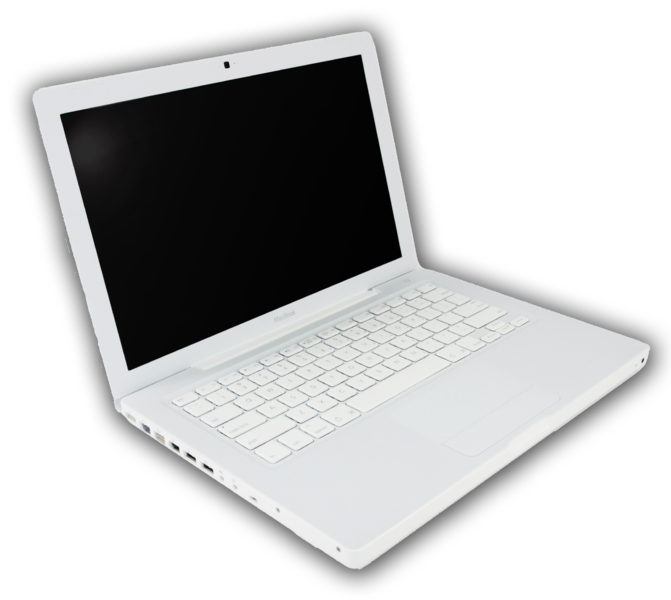
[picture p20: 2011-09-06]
Documentation/Images/hardware_layout/671px-MacBook_white.png

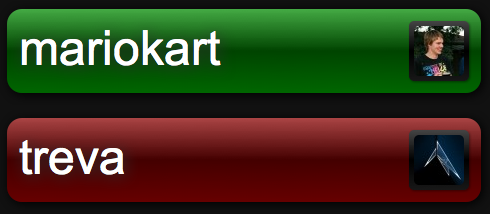
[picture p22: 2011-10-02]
Documentation/ScientificReport/Wim/images/joe-dashboard.png

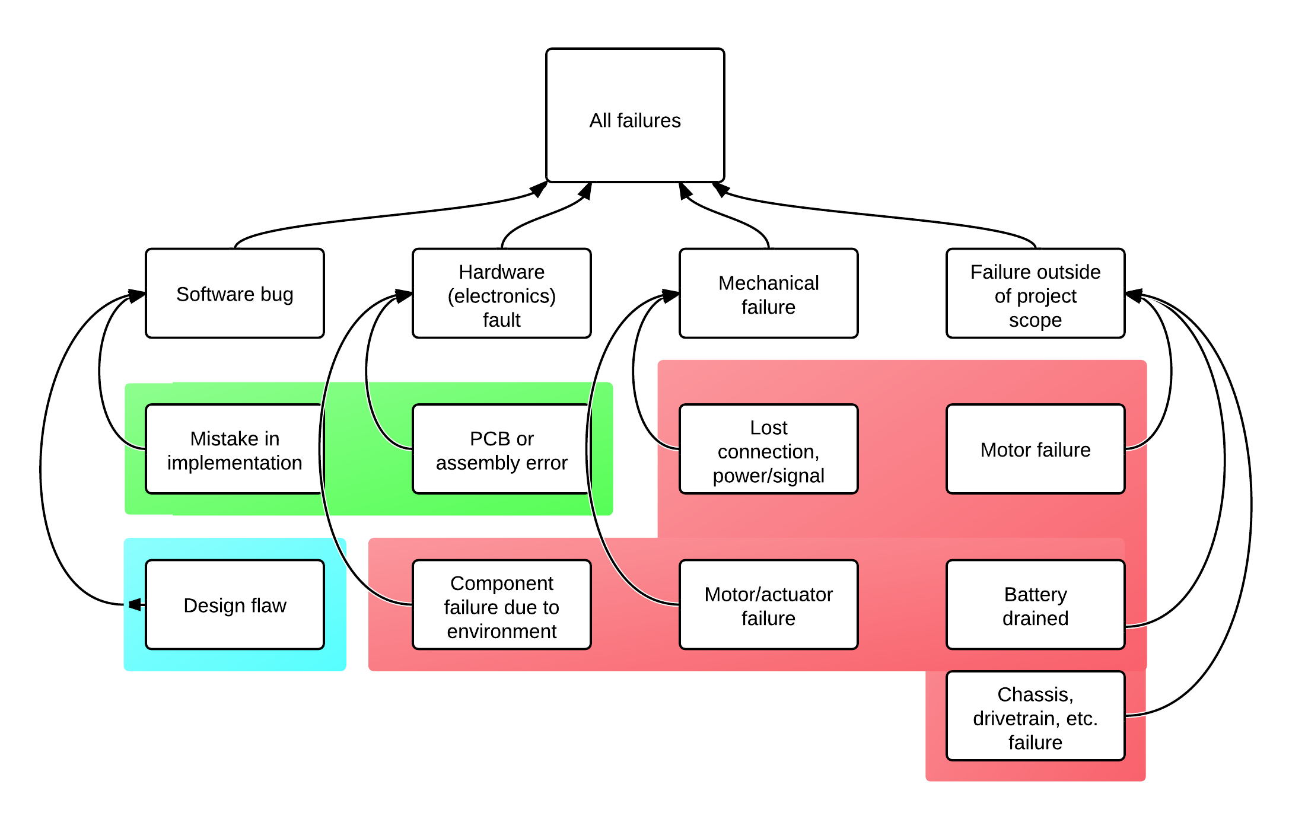
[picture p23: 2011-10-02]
Documentation/ScientificReport/Simon/FailTree.png

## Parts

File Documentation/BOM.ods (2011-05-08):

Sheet: Sheet1
 | Part Number | Description | Order Location | Quantity | Cost Per Unit | Subtotal
Steering | IG52 – 04 | 24VDC 10rpm Gear Motor with Encoder | http://superdroidrobots.com | 1 | $185.00 | $185.00
 | Shipping | Gear Motor Shipping |  | 1 | $75.00 | $75.00
 |  | Motor Driver |  | 1 | $0.00 | $0.00
 |  | Mounting Bracket | ECE Department | 1 | $50.00 | $50.00
Breaking | 5 1752 | 4 inch stroke 100lb 24VDC Linear actuator | http://surpluscenter.com | 1 | $50.00 | $50.00
 | Shipping | Linear actuator Shipping |  | 1 | $50.00 | $50.00
 |  | Mounting Bracket | ECE Department | 1 | $50.00 | $50.00
Accelerator | ATMEGA8L-8PU | Interface to go-kart power control | Digikey | 1 | $5.16 | $5.16
 | LM317KCS | IC VOLT REG POS ADJ 3TERM TO-220 | Digikey | 1 | $1.13 | $1.13
 |  | PCB | ECE Department | 1 | $20.00 | $20.00
CAN Bus | PL-STP6-0 | DYNAMIX 0.5M Cat6 Beige STP Patch Lead (CAN Bus) | http://www.cablesdirect.co.nz | 3 | $4.50 | $13.50
 | PL-STP6-1 | DYNAMIX 1.0M Cat6 Beige STP Patch Lead (CAN Bus) | http://www.cablesdirect.co.nz | 1 | $5.70 | $5.70
 | SS60000-009G | RJ45 CONN MOD JACK 8-8 SHLD EPP918A (CAN Input/output) | Digikey | 10 | $4.96 | $49.60
 | Header 10X2 | Header, 10-Pin, Dual row (JTAG ) | ECE Store | 5 | $1.00 | $5.00
 | fdd8445 | N-Channel PowerTrench® MOSFET 40V, 50A, 8.7mΩ | ECE Store | 5 | $2.00 | $10.00
 | SW-PB | Switch (Reset) | ECE Store | 5 | $3.00 | $15.00
 | AT91SAM7X256-AU | Smart ARM Microcontroller, ARM7TDMI 32-Bit RISC CPU, 256KB Flash and 64KB SRAM | Digikey | 5 | $19.37 | $96.85
 | ATA6660-TAPY-19 | Network Controller & Processor ICs High Speed CAN Transceiver | http://nz.mouser.com | 5 | $2.47 | $12.35
 | AE9925-ND | USB Type B connector | ECE Store | 5 | $1.52 | $7.60
 | MCP130T-300I/TT | Microcontroller Supervisory Circuit with Open Drain Output, 3-Pin SOT-23, Industrial Temperature, Tape and Reel | Digikey | 5 | $0.76 | $3.80
 |  | PCBs | Advanced Circuits | 1 | $217.00 | $217.00
Other |  | Misc Components (Diodes, Resistors, Capacitors, Wire, Headers) | ECE Store | 1 | $60.00 | $60.00
 | Shipping | Component Shipping from Digikey and Element14 |  | 1 | $30.00 | $30.00
 |  |  |  | 1 | $0.00 | $0.00
 |  |  |  |  | Total | $1,012.69

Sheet: Sheet2
 |  | 24VDC 10rpm Gear Motor with Encoder
 | Shipping | Gear Motor Shipping
 |  | Motor Driver |  | 1 | $0.00
 |  | Mounting Bracket | ECE Department | 1 | $50.00
 |  | 4 inch stroke 100lb 24VDC Linear actuator | http://surpluscenter.com | 1 | $50.00
 | Shipping | Linear actuator Shipping |  | 1 | $50.00
 |  | Mounting Bracket | ECE Department | 1 | $50.00
 | ATMEGA8L-8PU | Interface to go-kart power control | Digikey | 1 | $5.16
 | LM317KCS |  | Digikey | 1 | $1.13
 |  | PCB | ECE Department | 1 | $20.00
 | PL-STP6-0 | DYNAMIX 0.5M Cat6 Beige STP Patch Lead (CAN Bus) | Element14 | 3 | $4.50
 | PL-STP6-1 | DYNAMIX 1.0M Cat6 Beige STP Patch Lead (CAN Bus) | Element14 | 1 | $5.70
 | SS60000-009G | RJ45 CONN MOD JACK 8-8 SHLD EPP918A (CAN Input/output) | Digikey | 10 | $4.96
 | Header 10X2 | Header, 10-Pin, Dual row (JTAG ) | ECE Store | 5 | $1.00
 | ZXM61N03FTA | N-Channel PowerTrench® MOSFET 40V, 50A, 8.7mΩ | ECE Store | 5 | $2.00
 | SW-PB | Switch (Reset) | ECE Store | 5 | $3.00
 | AT91SAM7X256-AU | Smart ARM Microcontroller, ARM7TDMI 32-Bit RISC CPU, 256KB Flash and 64KB SRAM | Digikey | 5 | $19.37
 | ATA6660-TAPY-19 | Network Controller & Processor ICs High Speed CAN Transceiver | U2 | 5 | $2.47
 | AE9925-ND | USB Type B connector | ECE Store | 5 | $1.52
 | MCP130T-300I/TT | Microcontroller Supervisory Circuit with Open Drain Output, 3-Pin SOT-23, Industrial Temperature, Tape and Reel | Digikey | 5 | $0.76
 |  | PCBs | Advanced Circuits | 1 | $217.00
Other |  | Misc Components (Diodes, Resistors, Capacitors, Wire, Headers) | ECE Store |  | $60.00
 | Shipping | Component Shipping from Digikey and Element14 |  |  | $30.00
 |  |  |  | 1 | $0.00

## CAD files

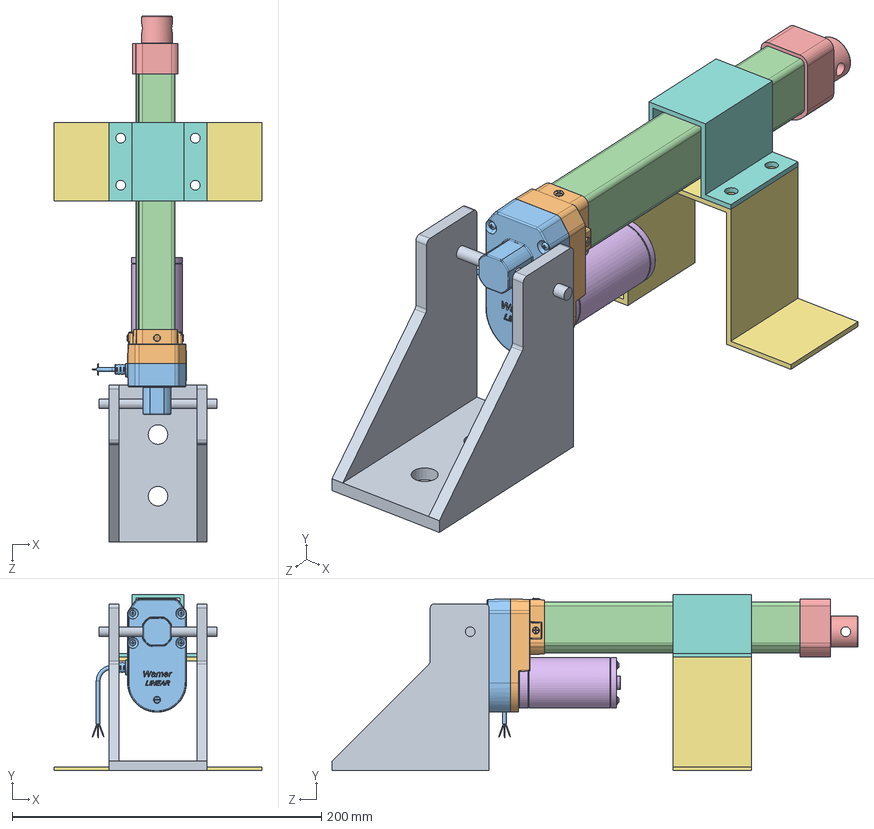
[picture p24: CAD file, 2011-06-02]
CAD/linear actuator/actuator_in_bracket.SLDASM
134.6 x 114.2 x 340.3 mm
actuator_bracket
M-TRACK_BASEPLATE
M-TRACK_GEARBOX-COVER
AP4
M-TRACK_SEAL
M-TRACK_CYLINDER
positioning_bracket
top_bracket

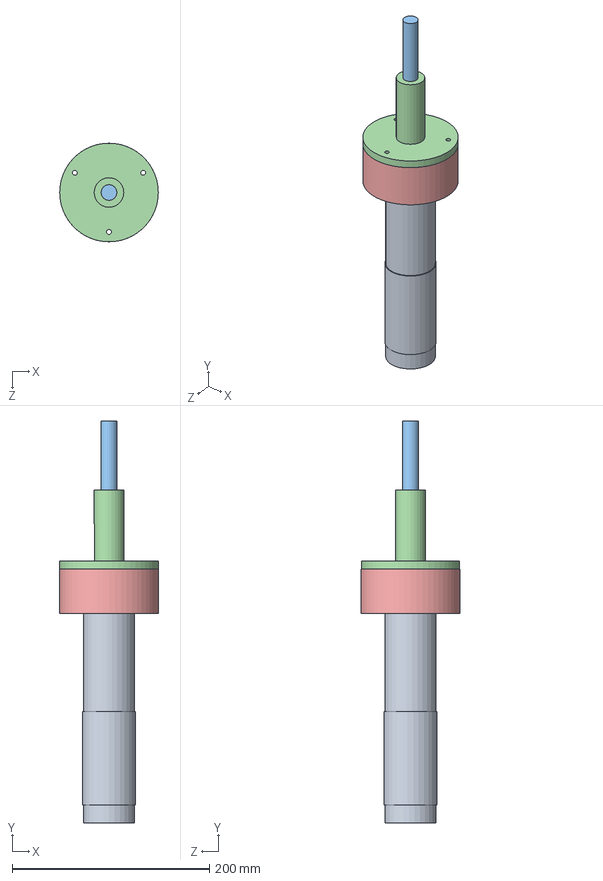
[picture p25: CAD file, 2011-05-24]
CAD/Steering bracket/Assem1.SLDASM
100.0 x 407.5 x 100.0 mm
steering motor
Motor connector
Drive shaft
Shaft bracket
Motor bracket

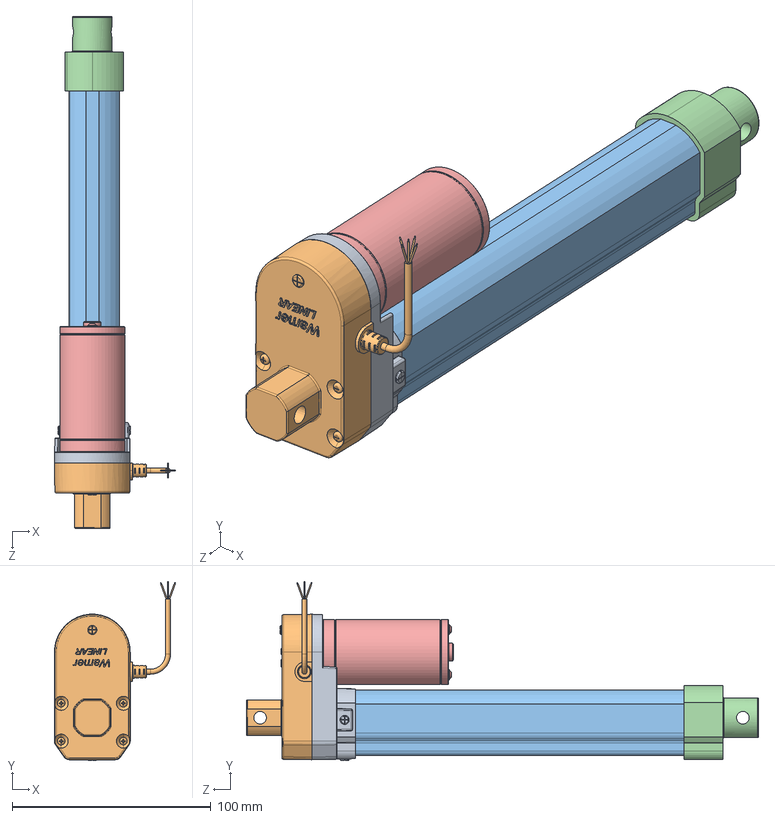
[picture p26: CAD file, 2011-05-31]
CAD/linear actuator/linear actuator.sldasm
61.1 x 90.3 x 257.8 mm
M-TRACK_BASEPLATE
M-TRACK_GEARBOX-COVER
AP4
M-TRACK_SEAL
M-TRACK_CYLINDER

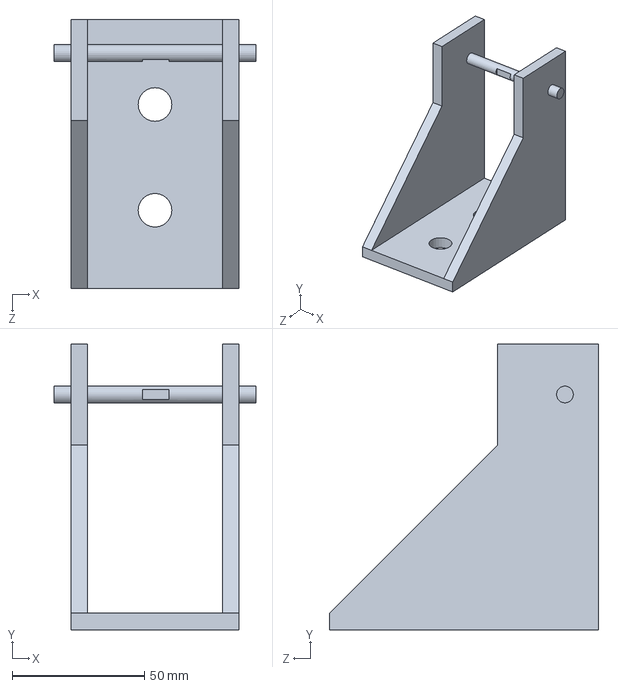
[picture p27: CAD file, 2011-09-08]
CAD/linear actuator/actuator_bracket.SLDPRT
76.2 x 108.0 x 101.6 mm

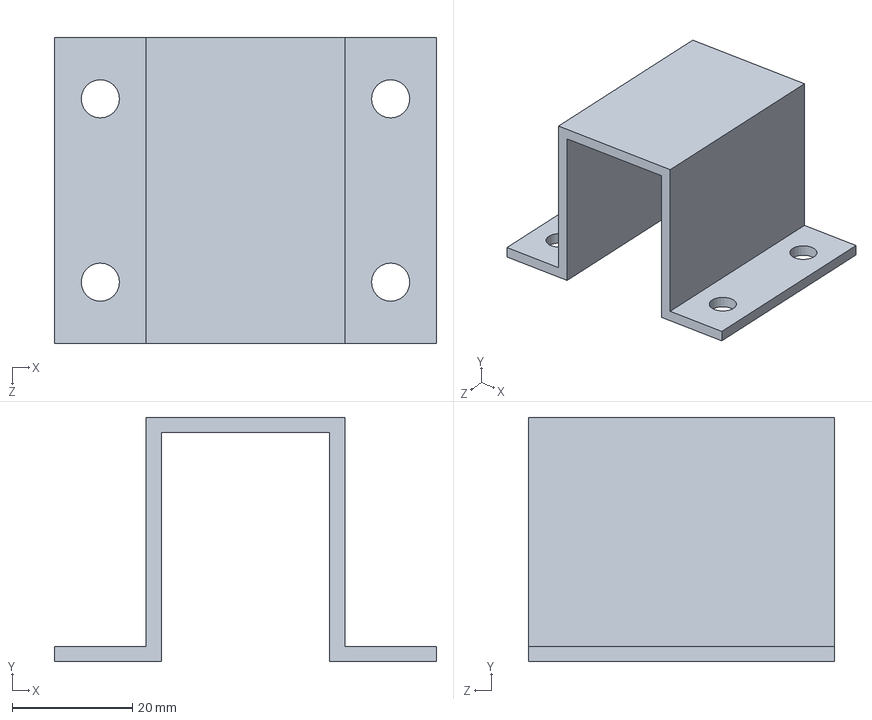
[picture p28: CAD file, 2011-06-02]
CAD/linear actuator/top_bracket.SLDPRT
63.5 x 40.6 x 50.8 mm

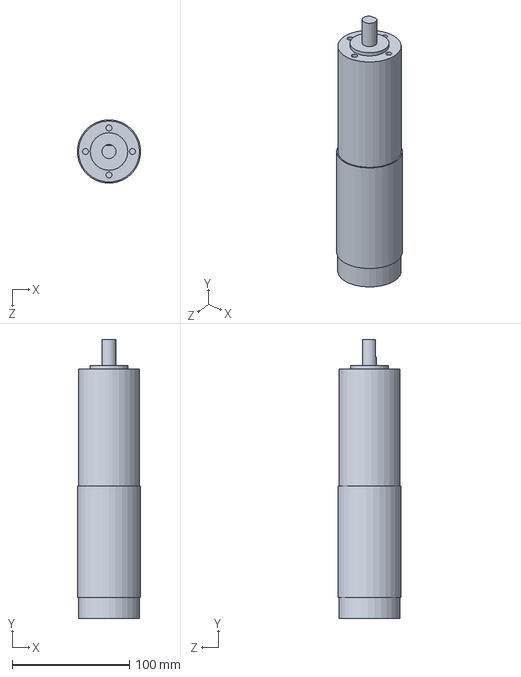
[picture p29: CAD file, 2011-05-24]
CAD/Steering bracket/steering motor.SLDPRT
53.7 x 237.5 x 54.0 mm

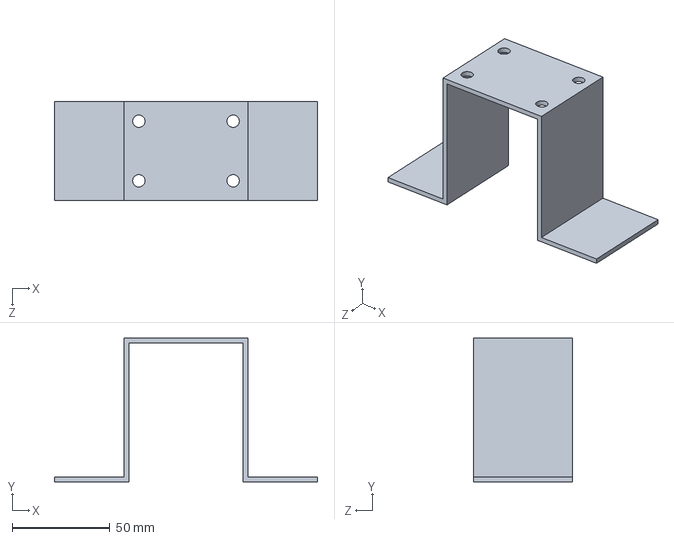
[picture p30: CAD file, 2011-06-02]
CAD/linear actuator/positioning_bracket.SLDPRT
134.6 x 73.7 x 50.8 mm

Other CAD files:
CAD/Steering bracket/Motor bracket.sldprt
CAD/linear actuator/M-TRACK_SEAL.sldprt
CAD/Steering bracket/Motor connector.sldprt
CAD/Steering bracket/Drive shaft.sldprt
CAD/linear actuator/M-TRACK_GEARBOX-COVER.sldprt
CAD/Steering bracket/Shaft bracket.sldprt
CAD/linear actuator/M-TRACK_BASEPLATE.sldprt
CAD/linear actuator/M-TRACK_CYLINDER.sldprt
CAD/linear actuator/AP4.sldprt
CAD/linear actuator/m1-d024-0100-a04-lp.stp
CAD/linear actuator/actuator_in_bracket.x_t
CAD/linear actuator/assembly_drawing.SLDDRW

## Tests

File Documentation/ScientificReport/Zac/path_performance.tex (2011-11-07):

\section{Performance of Path Following}

Due to delays in the project converting the go-kart to a point where it could be interfaced with the laptop the algorithm was never tested on the kart. To allow for some basic testing a simple GUI output was instead added to the program. This mapped the absolute location of the kart and the chessboard as well as the path they had taken. It also highlighted the point which the kart was currently driving towards. Fake input from the steering and speed sensors were created giving the kart a constant speed and a maximum turn rate of 30 degrees per second. This system is shown in Figure~\ref{tracking}. This interface allowed the system to be debugged and tested though was fairly limited in comparison to the actual go-kart. Its largest problem was that as the system believed that it was moving forward and turning it saw a stationary marker in front of it as moving to maintain the same relative position. This meant that testing the system's ability to follow patterns laid out by the marker was seriously hindered.

\begin{figure}[ht]
	\begin{center}
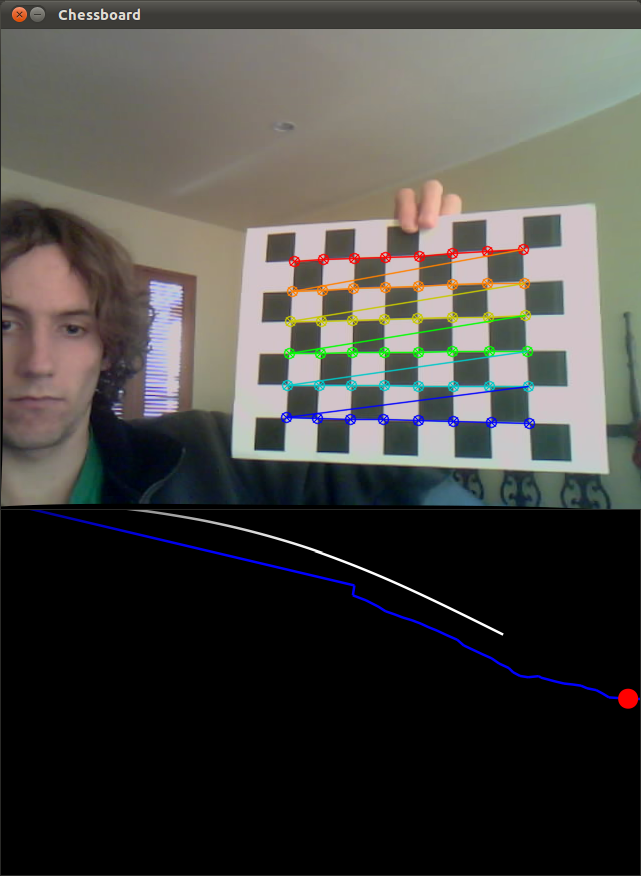
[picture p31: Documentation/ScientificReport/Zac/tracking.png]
		
	\end{center}
	\caption{Path finding GUI using chessboard detection. The path of the kart is shown in white, blue for the chessboard and the red dot is the current point the kart is driving towards}
	\label{tracking}
\end{figure}

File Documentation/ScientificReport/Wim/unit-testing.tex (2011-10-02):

\subsection{Unit Testing}

  As mentioned earlier Unit Testing is currently seeing a major increase in use
  in forward-thinking software development companies, mainly because of
  evangelical Agile development proponents (especially from the Ruby on Rails
  community).  Unfortunately despite this increase for traditional software
  development, the uptake in embedded development projects has been a lot
  slower.

  The basic premise of unit testing is that if you verify that all parts of your
  system work as intended, then the system as a whole will work as intended.  To
  do the verification you write a lot of small \emph{unit} tests to verify
  minimal sections of your code.  By ensuring that all code you write is tested
  by multiple unit tests you can be confident that the code performs as you
  expect.

  Of course this isn't the same thing as being right, unit tests only verify
  that the code does what the test says it should.  To ensure the code does what
  it should do you need to validate your tests.  This is most commonly done
  informally, the test developers know the intended outcome and write the tests
  with the codes final purpose in mind.  For more critical systems an external
  validation can be performed using a method such as modelling.  Our attempts at
  modelling one of the critical sections of our system can be read about in
  \emph{Safety by Design for the Mariokart System} by Simon Richards
  \cite{Richards_2011}.

  The big problem with unit testing an embedded system is the very low level of
  abstraction.  One of the big reasons it is so popular in the Ruby on Rails
  community is because of how easy it is to write tests for Ruby thanks to its
  very high level of abstraction.  For embedded development you are likely going
  to want to run a few different testing layers; one testing the very low level
  libraries to ensure the registers are being accessed correctly, one testing
  mid level libraries such as character or LCD displays to make sure they're
  calling the low level libraries properly and one testing the actual
  application code.

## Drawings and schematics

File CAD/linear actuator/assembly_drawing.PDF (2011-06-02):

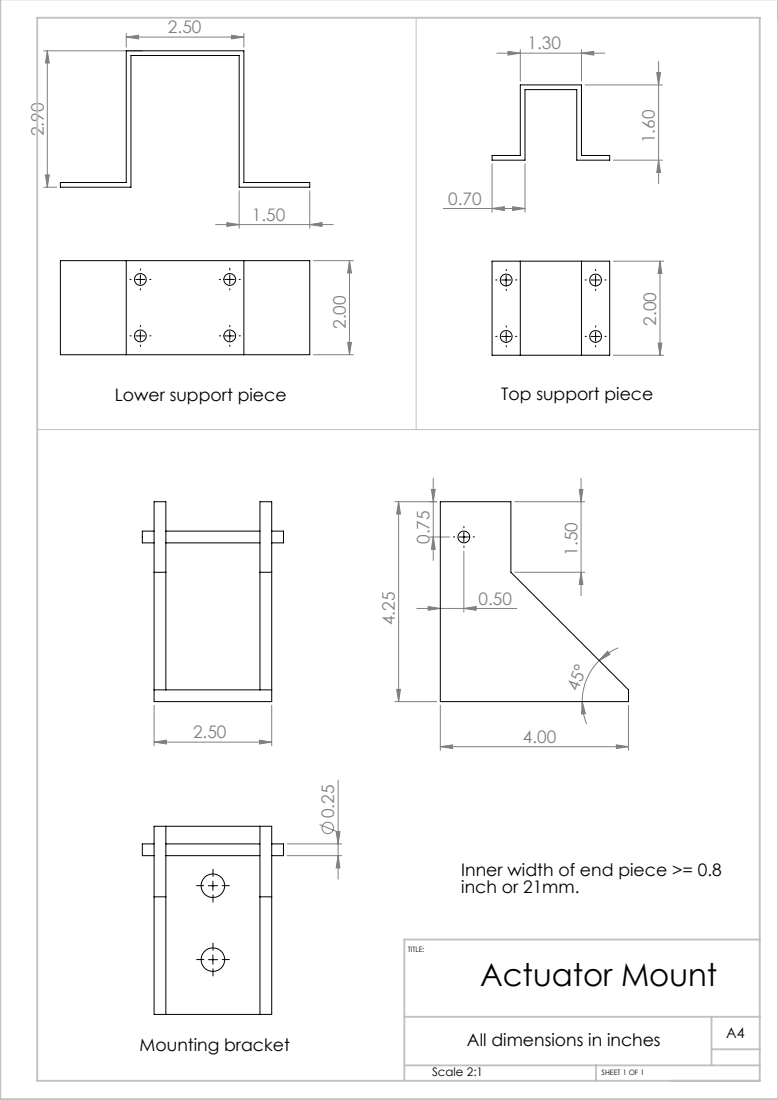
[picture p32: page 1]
Mounting bracket; SHEET 1 OF 1; Scale 2:1

Top support piece

Lower support piece

Inner width of end piece >= 0.8
inch or 21mm.
Actuator Mount

All dimensions in inches

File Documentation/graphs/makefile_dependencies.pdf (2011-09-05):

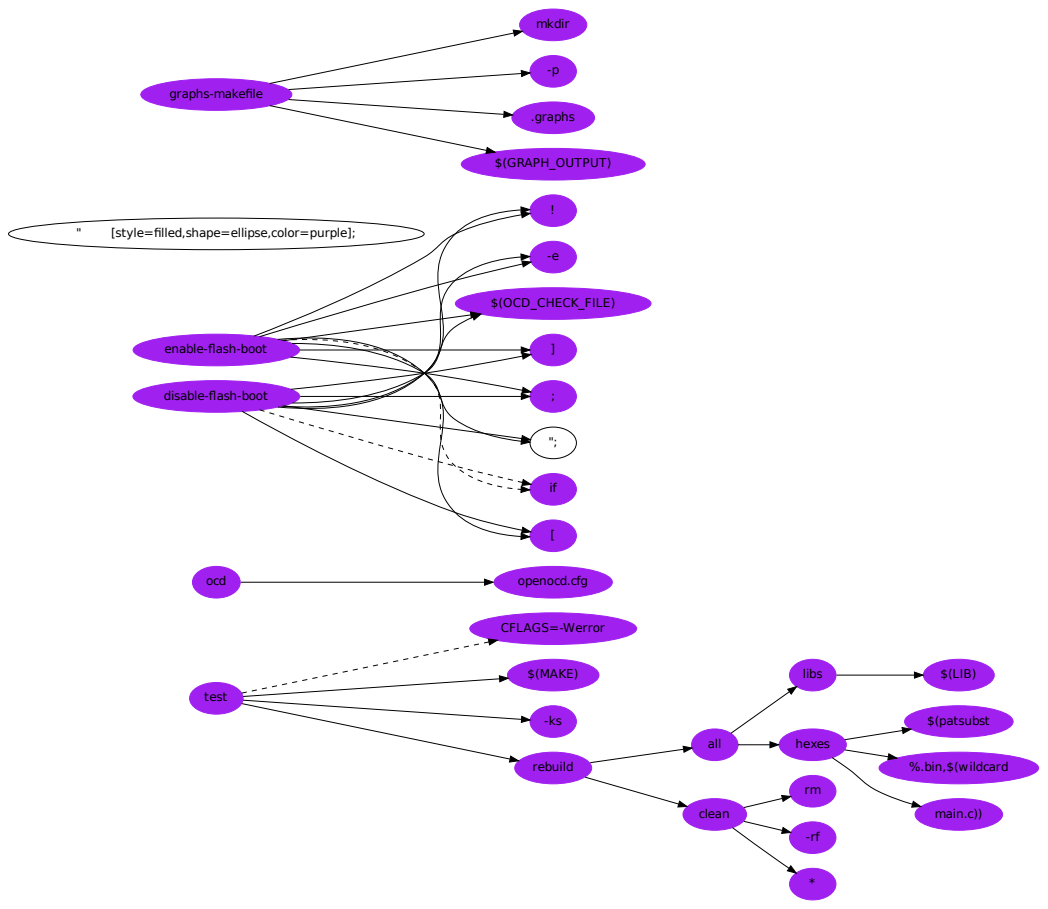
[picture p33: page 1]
libs; $(LIB); $(patsubst; %.bin,$(wildcard; main.c)); all; hexes; CFLAGS=-Werror; $(MAKE); clean; rebuild; test; ocd; openocd.cfg; $(OCD_CHECK_FILE); [style=filled,shape=ellipse,color=purple];; mkdir; .graphs; $(GRAPH_OUTPUT); graphs-makefile

enable-flash-boot

disable-flash-boot

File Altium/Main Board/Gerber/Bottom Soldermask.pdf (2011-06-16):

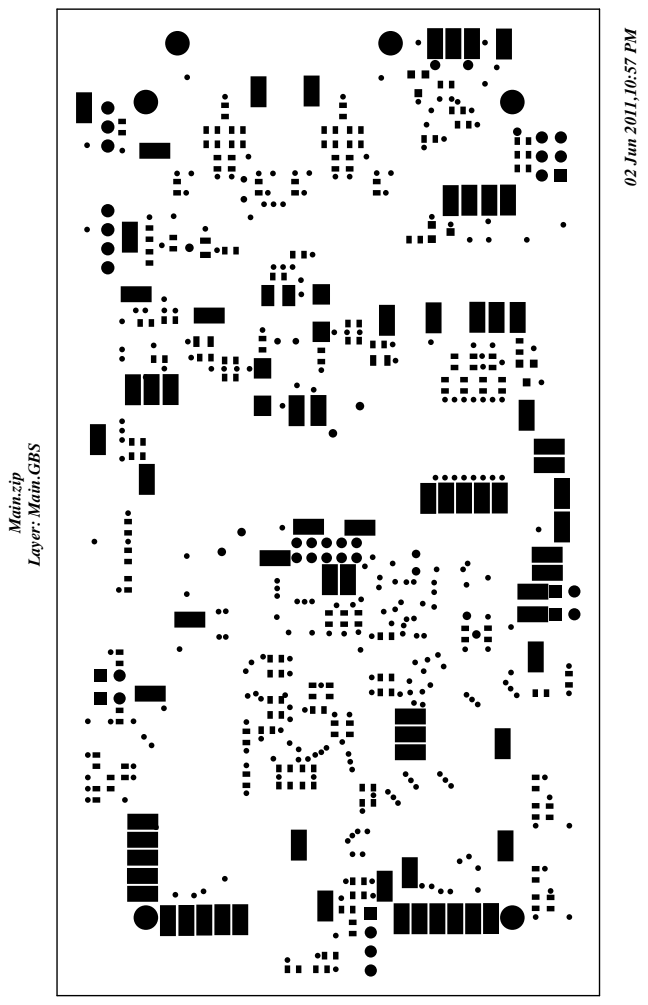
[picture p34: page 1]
Main.zip; 02 Jun 2011,10:57 PM

Layer: Main.GBS

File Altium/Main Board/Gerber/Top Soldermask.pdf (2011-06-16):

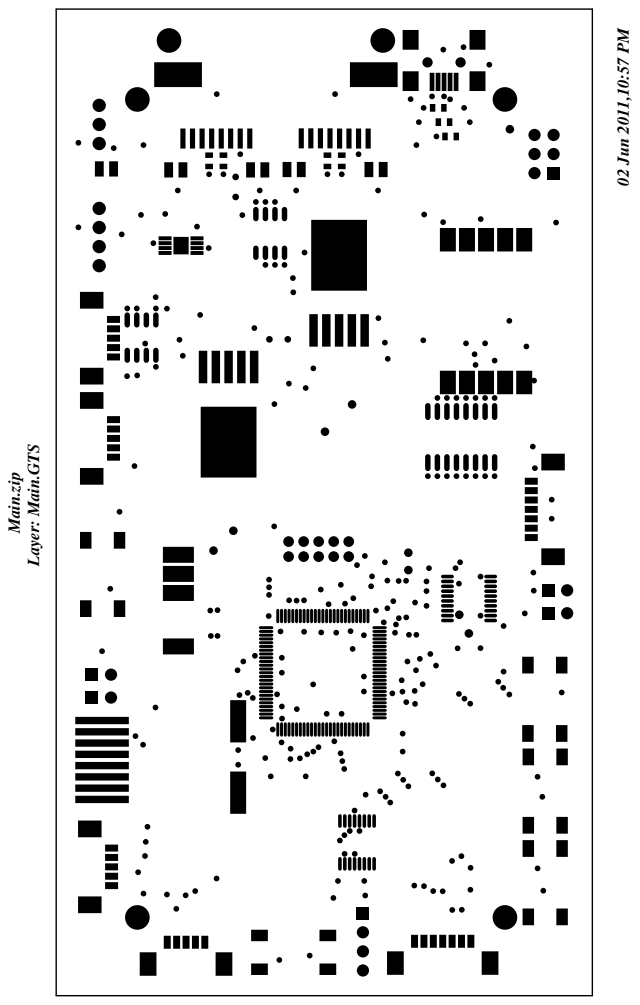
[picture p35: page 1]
Main.zip; 02 Jun 2011,10:57 PM

Layer: Main.GTS

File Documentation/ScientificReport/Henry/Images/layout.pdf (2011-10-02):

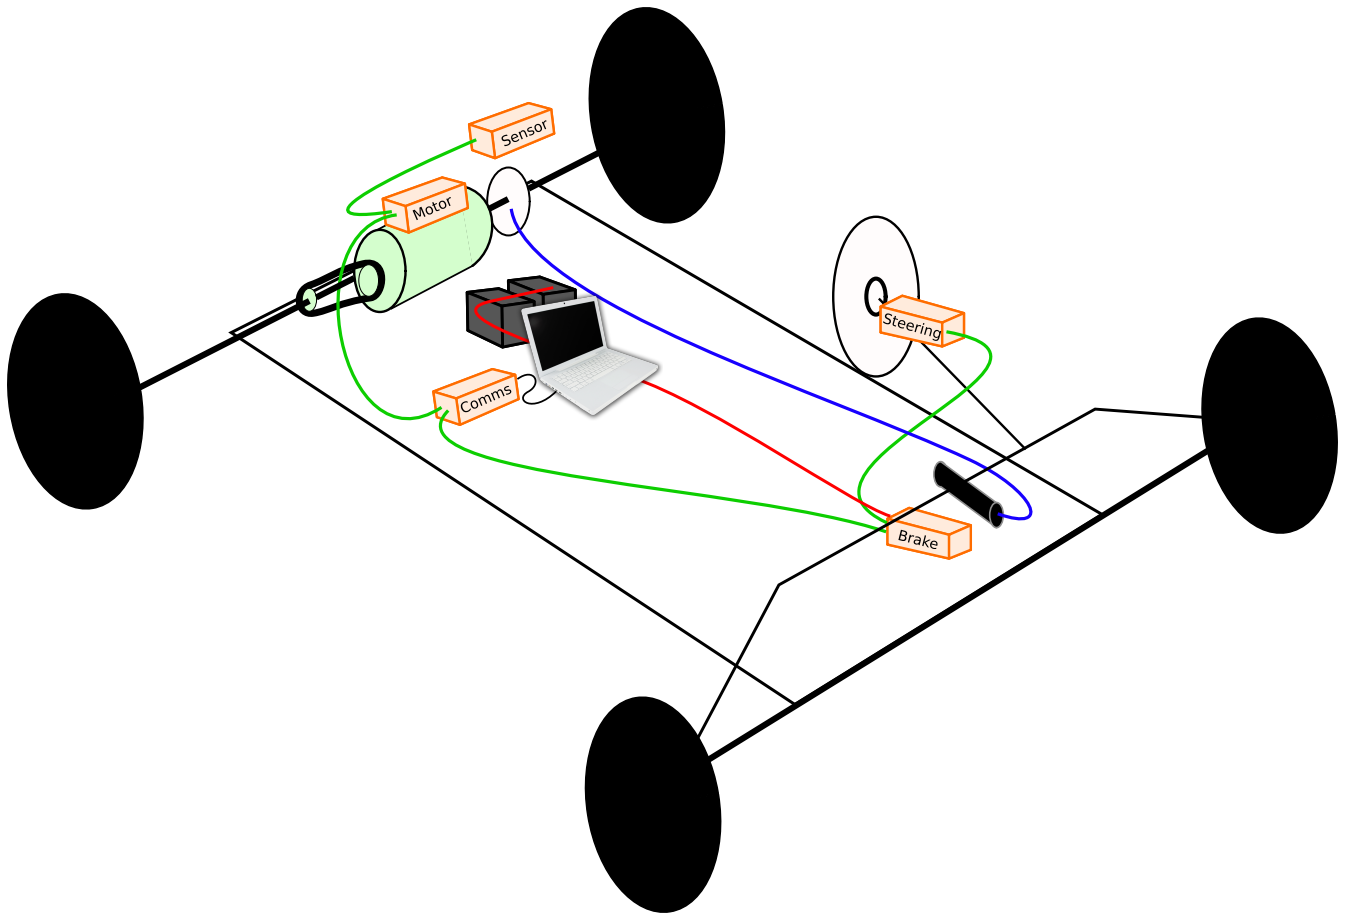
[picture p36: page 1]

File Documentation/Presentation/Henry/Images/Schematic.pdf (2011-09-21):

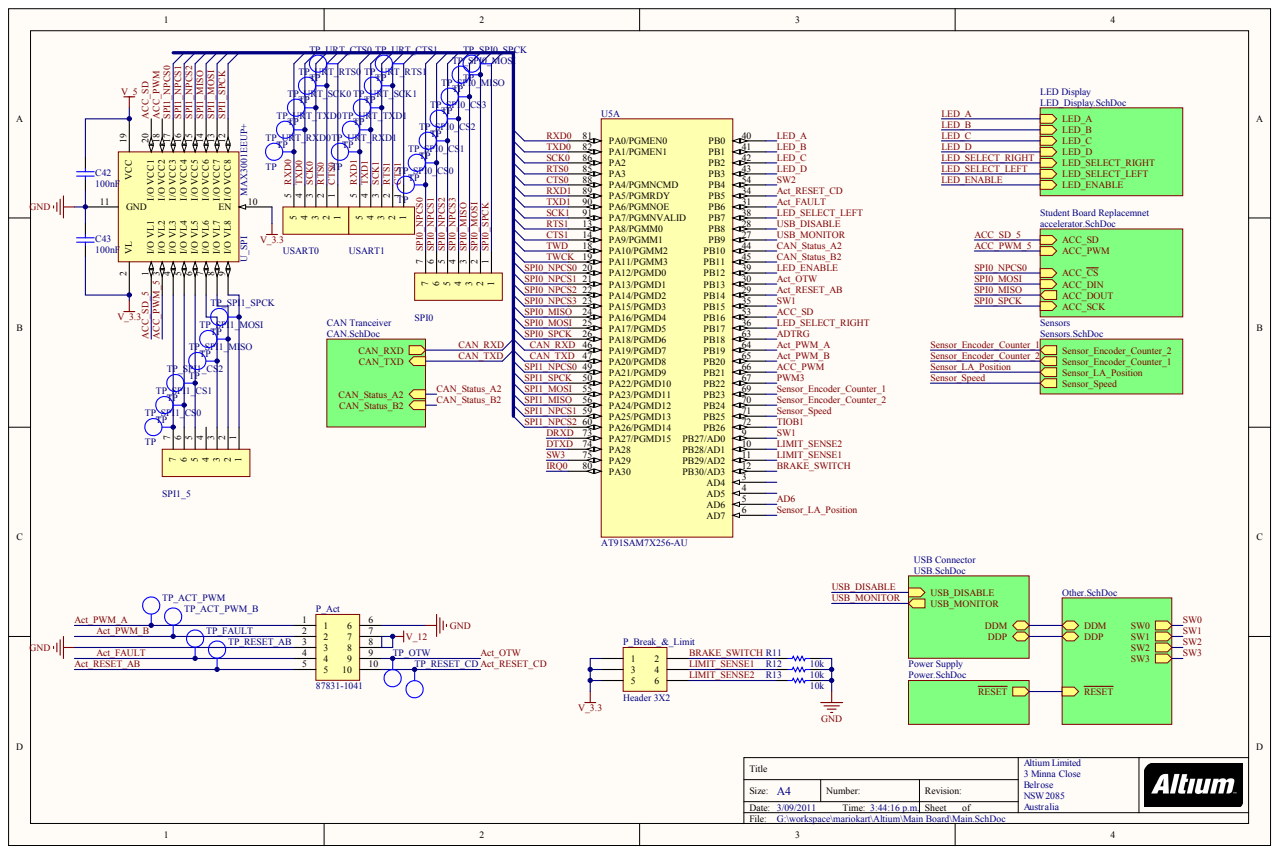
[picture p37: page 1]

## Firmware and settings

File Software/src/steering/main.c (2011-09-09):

/* ----------------------------------------------------------------------------
 *          Mariokart project
 * ----------------------------------------------------------------------------
 *  Copyright (c) 2011, University of Canterbury
 */

//------------------------------------------------------------------------------
//         Headers
//------------------------------------------------------------------------------
#include <actuator_driver.h>
#include <components/char_display.h>
#include <components/debug.h>
#include <components/switches.h>
#include <tc/tc.h>
#include <encoder.h>
#include <protocol/protocol.h>
#include <pio/pio.h>
#include <pio/pio_it.h>

//------------------------------------------------------------------------------
//         Local defines
//------------------------------------------------------------------------------
#define SOFTWARE_NAME "Steering"

//angle in degrees that the wheel may come within the end of its travel
//due to some round processes in converting from pulses to degrees this 
//must not be set to 0
#define SAFETY_MARGIN 10

//TODO:reenable PWM commands
#define DISABLE_PWM

//------------------------------------------------------------------------------
//         Local variables
//------------------------------------------------------------------------------
//minimum angle wheel can be turned to in degrees
int steering_min_angle;

//maximum angle wheel can be turned to in degrees
int steering_max_angle;

//location of wheel measured in pulses from encoder
int steering_loc_in_pulses = 0;

//sets pins of limit switches
const Pin pin_lim_up = LIM_SW_UP;
const Pin pin_lim_down = LIM_SW_DOWN;

typedef enum {
    UNCALIBRATED,
    FINDING_ANTICLOCK,
    FINDING_CLOCK,
    CENTERING,
    SETTING_SWITCHES,
    CALIBRATED
} cal_state;

//------------------------------------------------------------------------------
//         Interrupt Handlers
//------------------------------------------------------------------------------
//triggers error on limit switches (ISR must not be set till after calibration)

void LIMIT_ISR(const Pin *pin) {
    if (!PIO_Get(&pin_lim_up) || !PIO_Get(&pin_lim_down)) {
        //something wrong with steering so stops motor
        act_driver_drive(0);

        TRACE_WARNING("LIMIT SWITCH ACTIVATED ENTERING ERROR STATE\r\n");
        proto_state_error();
    }
}

void timer_callback() {
    char_display_tick();
}

//------------------------------------------------------------------------------
//         Local Functions
//------------------------------------------------------------------------------
//sets steering to an angle (in degrees) between min_angle and max_angle

void set_steering(int angle) {

    angle = angle + ((steering_max_angle - steering_min_angle) / 2) + steering_min_angle;

    if (angle > steering_max_angle - SAFETY_MARGIN) {
        angle = steering_max_angle - SAFETY_MARGIN;
    } else if (angle < steering_min_angle + SAFETY_MARGIN) {
        angle = steering_min_angle + SAFETY_MARGIN;
    }

    //convert angle to pulses and account for any offset
    steering_loc_in_pulses = (angle * ENCODER_PULSES_PER_REV) / 360;

}

//gets the steering wheels current position in degrees

int get_steering_pos(void) {
    return (((encoder_position_output * 360.0) / ENCODER_PULSES_PER_REV)) -
            ((steering_max_angle - steering_min_angle) / 2) - steering_min_angle;
}

//gets where the steering wheel is moving to in degrees

int get_steering_desired_pos(void) {
    return (((steering_loc_in_pulses * 360.0) / ENCODER_PULSES_PER_REV) -
            ((steering_max_angle - steering_min_angle) / 2)) -steering_min_angle;
}

//sets up the limit swiches interrupts

void steering_limit_sw_init(void) {

    // Initialize interrupts
    PIO_ConfigureIt(&pin_lim_up, LIMIT_ISR);
    PIO_ConfigureIt(&pin_lim_down, LIMIT_ISR);
    PIO_EnableIt(&pin_lim_up);
    PIO_EnableIt(&pin_lim_down);

    TRACE_INFO("Limit switch ISR activated\n\r");

}

//calibrates steering position by finding locaiton of limit switches and
//assuming straight ahead is halfway between them

void cal_steering(cal_state* cal) {

    switch (*cal) {
        case UNCALIBRATED:

            TRACE_INFO("Steering calibration started\n\r");
            *cal = FINDING_ANTICLOCK;
            break;

        case FINDING_ANTICLOCK:
            //drive steering anticlockwise until limit hit

            act_driver_drive(-50);

            if (PIO_Get(&pin_lim_down)) {
                //stop motor
                act_driver_drive(0);

                //record value in degrees
                steering_min_angle = 360 * encoder_position_output / ENCODER_PULSES_PER_REV;
                TRACE_INFO("Anticlockwise limit found at %i degrees\n\r", steering_min_angle);
                *cal = FINDING_CLOCK;
            }
            break;

        case FINDING_CLOCK:
            //drive steering clockwise until limit hit
            act_driver_drive(50);
            if (PIO_Get(&pin_lim_up)) {
                //stop motor
                act_driver_drive(0);

                //record value in degrees
                steering_max_angle = 360 * encoder_position_output / ENCODER_PULSES_PER_REV;
                TRACE_INFO("Clockwise limit found at %i degrees\n\r", steering_max_angle);

                //set starting position to center position
                set_steering(0);

                //check motor direction and enter error state if required
                if (steering_max_angle < steering_min_angle) {
                    TRACE_INFO("ERROR MOTOR SPINNING BACKWARDS\n\r");

                    //implement error state
                    proto_state_error();
                }
                TRACE_INFO("Center offset found to be %i degrees\n\r",
                        ((steering_max_angle - steering_min_angle) / 2) + steering_min_angle);

                //dont return until motor driven back to center
                TRACE_INFO("desired location %i, current location %i\n\r", get_steering_desired_pos(), get_steering_pos());
                act_driver_drive(-50);

                *cal = CENTERING;
            }
            break;

        case CENTERING:
            if (get_steering_pos() <= get_steering_desired_pos()) {
                //stop motor
                act_driver_drive(0);
                TRACE_INFO("Steering centered calibration finished\n\r");
                *cal = SETTING_SWITCHES;
            }
            break;

        case SETTING_SWITCHES:
            TRACE_INFO("Activating limit switch ISR \n\r");
            steering_limit_sw_init();
            *cal = CALIBRATED;
            break;
        default:
            proto_state_error();
            break;
    }

}

void send_ack(message_t orig_msg) {
    message_t msg = {
        .from     = ADDR_STEERING,
        .to       = orig_msg.from,
        .command  = CMD_ACK_SET,
        .data[0]  = orig_msg.data[0],
    };
    proto_write(msg);
}

//------------------------------------------------------------------------------
//         Main Function
//------------------------------------------------------------------------------

int main(int argc, char *argv[]) {
    debug_init(SOFTWARE_NAME);

    TRACE_INFO("Start steering board initialization\n\r");
    //enables interrupts (note resets all configured interrupts)
    PIO_InitializeInterrupts(AT91C_AIC_PRIOR_LOWEST);

    //Main initialisations
    char_display_init();
    switches_init();
    encoder_init();
#ifndef DISABLE_PWM
    act_driver_init();
#endif

    // Starts a 100Hz timer
    TC_PeriodicCallback(100, timer_callback);

    //sets pins as inputs
    PIO_Configure(&pin_lim_up, 1);
    PIO_Configure(&pin_lim_down, 1);

    proto_init(ADDR_STEERING);

#ifndef DISABLE_PWM
    int speed;
    cal_state cal = UNCALIBRATED;
#endif
    message_t msg;

    TRACE_INFO("Steering board initialization completed\n\r");

    while (1) {
        switch (proto_state()) {
            case STARTUP:
                break;
            case CALIBRATING:
                if (switches_pressed(0)) { //cal == CALIBRATED) {
                    proto_calibration_complete();
                } else {
#ifndef DISABLE_PWM
                    cal_steering(&cal);
#endif
                }
                break;
            case RUNNING:

                msg = proto_read();
                switch (msg.command) {
                    case CMD_SET:
                        set_steering(msg.data[0]);
                        send_ack(msg);
                        proto_refresh();
                    case CMD_NONE:
                        break;
                    default:
                        TRACE_WARNING("Invalid command %i received in running state", msg.command);
                        proto_state_error();
                        break; //ERROR?
                }
#ifndef DISABLE_PWM
                speed = act_driver_pid(steering_loc_in_pulses, encoder_position_output);
                act_driver_drive(speed);
#endif

                break;
            default: // ERROR
                // do error stuff
                break;
        }
    }
    return 0;
}

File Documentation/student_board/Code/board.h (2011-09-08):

//ADC inputs
#define ACCEL_PIN 4
#define AVG_CURRENT_PIN 1
#define RAW_CURRENT_PIN 2


//Digital inputs
#define ESTOP_PIN PIND 
#define ESTOP_PORT PORTD
#define ESTOP_BIT 3
#define ESTOP_PRESSED bit_is_clear(ESTOP_PIN, ESTOP_BIT)

#define BRAKE_PIN PIND
#define BRAKE_PORT PORTD
#define BRAKE_BIT 2
#define BRAKE_PRESSED bit_is_clear(BRAKE_PIN, BRAKE_BIT)


//Outputs
#define PWM_DDR DDRB
#define PWM_PORT PORTB
#define PWM_BIT 1

#define SD_DDR DDRD
#define SD_PORT PORTD
#define SD_BIT 4

#define SPI_DDR DDRB
#define SPI_PORT PORTB
#define MISO_BIT 4


#define RGB_PORT PORTD
#define RGB_DDR DDRD
#define RED 7
#define GREEN 6
#define BLUE 5

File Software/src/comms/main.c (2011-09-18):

/* ----------------------------------------------------------------------------
 *          Mariokart project
 * ----------------------------------------------------------------------------
 *  Copyright (c) 2011, University of Canterbury
 */

//------------------------------------------------------------------------------
//         Headers
//------------------------------------------------------------------------------
#include <components/char_display.h>
#include <components/debug.h>
#include <components/switches.h>
#include <protocol/protocol_master.h>
#include <tc/tc.h>
#include <aic/aic.h>
#include <pio/pio.h>
#include <pio/pio_it.h>
#include <pmc/pmc.h>
#include <usb/device/cdc-serial/CDCDSerialDriver.h>
#include <usb/device/cdc-serial/CDCDSerialDriverDescriptors.h>
#include <utility/trace.h>
#include <pit/pit.h>
#include <better_can/can.h>

#include "usb.c"

//------------------------------------------------------------------------------
//         Local defines
//------------------------------------------------------------------------------
#define SOFTWARE_NAME "Comms"
#define ALL_CLIENTS ((1<<ADDR_BRAKE) | (1<<ADDR_MOTOR)| (1<<ADDR_STEERING) )

volatile bool timeout = false;

message_t brake_msg = {
    .from = ADDR_COMMS,
    .to   = ADDR_BRAKE,
    .command = CMD_SET,
    .data = {
        VAR_BRK_POS,
        0
    }
};
message_t steering_msg = {
    .from = ADDR_COMMS,
    .to   = ADDR_STEERING,
    .command = CMD_SET,
    .data = {
        VAR_STEERING_ANGLE,
        0
    }
};
message_t motor_msg = {
    .from = ADDR_COMMS,
    .to   = ADDR_MOTOR,
    .command = CMD_SET,
    .data = {
        VAR_SPEED,
        0
    }
};

typedef bool(*output_send_t)(void);

static volatile message_t received_ack;

static unsigned int transmission_wait = 0;

/**
 * Blocks until the most recent message sent or times out
 * @return true if the message sent, false otherwise
 */
bool wait_on_ack(message_t msg) {
    transmission_wait = 0;
    while ( (received_ack.from != msg.to) && (received_ack.data[0] != msg.data[0]) ) {
        if (transmission_wait > 3) {
            BCAN_AbortTransfer(0, msg.to);
            return false;
        }
    }
    return true;
}

bool send_brake_value(void) {
    proto_write(brake_msg);
    return wait_on_ack(brake_msg);
}

bool send_steering_value(void){
    proto_write(steering_msg);
    return wait_on_ack(steering_msg);
}

bool send_motor_value(void){
    proto_write(motor_msg);
    return wait_on_ack(motor_msg);
}

bool check_speed_timeout(void){
    return true;
}


void timer_callback(void) {
    static int i = 0;

    // Update the display
    char_display_tick();
    transmission_wait++;
    AT91C_BASE_TC1->TC_SR;
    if (i++ > 10) {
        // A flag used to run periodic events in the background
        timeout = true;
        i = 0;
    }
}


int main(int argc, char *argv[]) {
    debug_init(SOFTWARE_NAME);

    unsigned int num_output_boards = 3;
    output_send_t output_board_send[] = {
        send_motor_value,
        send_brake_value,
        send_steering_value,
    };

    //enables interrupts (note resets all configured interrupts)
    PIO_InitializeInterrupts(AT91C_AIC_PRIOR_LOWEST);

    TC_PeriodicCallback(100, timer_callback);

    //Main initialisations
    char_display_init();
    switches_init();

    UsbInit();

    proto_init(ADDR_COMMS);

    unsigned int responses;

    message_t msg, usb_msg;
    message_t broadcast_message = {
        .from     = ADDR_COMMS,
        .to       = ADDR_BROADCAST_RX,
        .command  = CMD_NONE,
        .data_len = 0
    };

    while(1) {    
        switch (proto_state()) {
            case STARTUP:
                // Probe all board periodically
                if (timeout) {
                    responses = 0;
                    broadcast_message.command = CMD_REQ_CALIBRATE;
                    proto_write(broadcast_message);
                    timeout = false;
                } 

                // Check any responses
                msg = proto_read();
                switch(msg.command) {
                    case CMD_ACK_CALIBRATE:
                        responses |= 1 << msg.from; 
                        break;
                    case CMD_NONE:
                        break;
                    default:
                        TRACE_ERROR("Invalid command %i received in startup state\n\r", msg.command);
                        proto_state_error();
                        break;
                }

                // Check to see if all boards have acked
                if (responses == ALL_CLIENTS) {
                    char_display_number(24);
                    broadcast_message.command = CMD_CALIBRATE;
                    proto_write(broadcast_message);
                    proto_state_transition(CALIBRATING);
                    responses = 0;
                }

                break;

            case CALIBRATING:
                // Request a transition periodically
                if (timeout) {
                    responses = 0;
                    broadcast_message.command = CMD_REQ_RUN;
                    proto_write(broadcast_message);
                    timeout = false;
                } 

                // Check any responses
                msg = proto_read();
                switch(msg.command) {
                    case CMD_NONE:
                        break;

                    // A board acked, add its bit to the response list
                    case CMD_ACK_RUN: 
                        responses |= 1 << msg.from; 
                        break;
                        
                    // A board is refusing the transition
                    case CMD_NO:
                        break;

                    // Invalid response
                    default:
                        TRACE_ERROR("Invalid command %i received in calibrating state\n\r", msg.command);
                        proto_state_error();
                        break;
                }

                // Check if all clients have acked
                if (responses == ALL_CLIENTS) {
                    broadcast_message.command = CMD_RUN;
                    proto_write(broadcast_message);
                    proto_state_transition(RUNNING);
                }

                break;

            case RUNNING: // Normal state

                usb_msg = UsbRead();
                if (usb_msg.command != CMD_NONE) {
                    proto_write(usb_msg);
                    // TODO
                    // Set setpoints
                    // Send set points
                    // Check for acks
                    // Receive data from sensor
                    // Forward sensor data to laptop

                    // Clear message
                    usb_msg.command = CMD_NONE;
                }
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

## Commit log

2011-04-21 Added the source code and schematics for student board
    These were given to us by Bill for our use
    [GOCARTPCB.PcbDoc, GO_CART.PrjPcb, GO_CART.SCHDOC]
2011-04-24 Started on the schematic and footprint for SAM7X256
    [MarioLib.PcbLib, MarioLib.SchLib]
2011-04-25 Added ATA6660 schematic and footprint
    [MarioLib.PcbLib, MarioLib.SchLib]
2011-04-25 Added the TL2575 schematic and footprint
    [MarioLib.PcbLib, MarioLib.SchLib]
2011-04-25 Started on the common parts of the board
    [Common.SchDoc]
2011-04-25 Fixed an error in the TL2575 schematic
    [Common.SchDoc, MarioLib.SchLib]
2011-04-25 Updated the SAM7X schematic
    [MarioLib.SchLib]
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2011-04-25 Spelling mistake in gitignore and gitattributes. Added the start of the Communication board
    [Comms.PrjPCB, Main.SchDoc]
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2011-04-26 Work on the schematics.
    Highlights:
    * Did most of the JTAG stuff, based off the Olimex SAM7-EX256
    Development board (http://www.olimex.com/dev/sam7-ex256.html)
    * Added a voltage supervisor like the one on the Olimex board.
    * Moved all the JTAG and uC power stuff to the common board since it's
    not going to change between boards.
    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
    [Common.SchDoc, Main.PcbDoc, Main.SchDoc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]
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2011-04-27 Re-arranged a lot of stuff. Added USB to the other schematic
    [Common.SchDoc, Comms.PrjPCB, Main.PrjPCB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]
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2011-04-29 After looking at the steering column I added a solidworks part with a few of the dimensions (keyway and shaft diamter) included.
    [steering_column_ending.SLDPRT]
2011-04-29 Photos of the steering column being dissasembled (or assembled if you watch it in reverse). Sorry about the size.
2011-04-29 Updated the Terminators to use the 9pin dbus
    [Terminators.PcbDoc, Terminators.SchDoc]
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2011-04-29 Adding some more capacitors for nicer bulk decoupling
    [Power.SchDoc]
2011-04-29 Updating the terminator pcb.\n\nHas been checked against FreedDFM and doesn't violate their rules.
    [Terminators.PcbDoc, Terminators.SchDoc]
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2011-05-07 Set up a folder for swrx files, moved current files to it
    [steering_column_ending.SLDPRT]
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2011-05-08 Added the BOM and screenshot of Gantt chart
    BOM is in open document spreadsheet format
    [BOM.ods]
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2011-05-11 added solidworks models of motor and linear actuator
    [AP4.sldprt, M-TRACK_BASEPLATE.sldprt, M-TRACK_CYLINDER.sldprt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]
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2011-05-15 Moved CAN Tranceiver to it's own board.
    Added termination selection via headers.
    [CAN.SchDoc, Main.PrjPCB, Main.SchDoc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]
2011-05-15 Changed to use 0Ω resistor for termination selection
    [CAN.SchDoc, Main.SchDoc, Other.SchDoc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]
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2011-05-16 Updated to what's on the paper we were given
    Changed to the rj45 connector
    Changed from rx/tx header to break input
    [GO_CART.SCHDOC]
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2011-05-17 added motor driver to main board and fixed it up a bit
    [Motor Driver.SchDoc, Steering Motor Driver.SchDoc]
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2011-05-17 Hooked up the reset pin and removed the old voltage regulator
    [Main.SchDoc, Other.SchDoc, Power.SchDoc]
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2011-05-19 more work on brcket and a bit on motor driver
    [Assem1.SLDASM, Drive shaft.sldprt, MarioLib.SchLib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]
2011-05-20 made motor board into its own project and added headers to it
    [Motor Board.PcbDoc, Motor Board.PrjPcb, Motor Driver.SchDoc]
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2011-05-23 Added student board replacement and accel
    This adds the schematic that allows us to replace the entire student
    board by porting the code that was given to us
    [Main.PrjPCB, Main.SchDoc, Sensor_Speed.SchDoc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]
2011-05-23 Lots of updates and additions to the powersupply
    [CAN.SchDoc, Main.SchDoc, MarioLib.SchLib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]
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2011-05-24 Added switchs LED Display power supply pins
    A couple of SPI, UART and GPIO headers need adding still
    [Main.PrjPCB, Main.SchDoc, Other.SchDoc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]
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2011-05-26 Updated the rules in the motor board pcb
    [Main.PrjPCB, Motor Board.PcbDoc, Motor Board.PrjPcb]
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2011-05-26 Added motor board connector to main board and cleaned up some stuff
    [CAN.SchDoc, Main.PrjPCB, Main.SchDoc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]
2011-05-26 Added the Molex 5 and 7 pin PicoBlade headers
    [MarioLib.SchLib]
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2011-05-26 Main schematic is nearly finished
    It is just missing the feedback from the motors
    [Main.SchDoc]
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2011-05-27 Updated the thermal vias to meet design rules
    [MarioLib.PcbLib]
2011-05-27 Done the SAM7X decoupling caps and voltage regulators
    [Main.PcbDoc]
2011-05-28 Added a lever shifter for the student board replacement
    [MarioLib.SchLib, accelerator.SchDoc]
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2011-05-28 fixed small error on encoder schematic
    [Sensors.SchDoc]
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2011-05-28 Updated names, added livelshifter for one of the SPI ports
    [CAN.SchDoc, Main.SchDoc, Power.SchDoc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]
2011-05-28 got rid of errors on motor board
    [Motor Board.PcbDoc]
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2011-05-29 There were some changes.
    Just continued work on the PCB and other schematoc parts
    [LED_Display.SchDoc, Main.PcbDoc, Main.SchDoc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]
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2011-05-30 Added supplier values to all parts. Lots of small changes!!!
    [CAN.SchDoc, LED_Display.SchDoc, Main.PcbDoc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]
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2011-05-31 changed to correct library and header for motor board
    [Motor Board.PcbDoc, Motor Driver.SchDoc]
2011-05-31 Updated the LED display to something that might work.
    [LED_Display.SchDoc]
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2011-05-31 Changes to the PCB mostly.
    Also changed the dirrection of ACC_PWM and ACC_SD
    [Main.PcbDoc, Main.PrjPCB, Main.SchDoc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]
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2011-05-31 Updated which headers are used for the sensors
    [Sensors.SchDoc]
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2011-05-31 Updated hole sizes for board to board header
    [MarioLib.PcbLib]
2011-05-31 Almost done, only 6 things to go.
    3 nets to route.
    2 disconnected plane pieces that don't matter.
    All the overlays need moving around.
    [Main.PcbDoc, Main.PrjPCB]
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2011-06-01 Added test points and cleaned up last air wires
    there are still a few rule errors on PCB
    [CAN.SchDoc, LED_Display.SchDoc, Main.PcbDoc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]
2011-06-02 Finished the actuator mount design. PDF provided for the SOlidworks-less.
    [M-TRACK_SEAL.sldprt, actuator_bracket.SLDPRT, actuator_in_bracket.SLDASM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]
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2011-06-02 Moved a swrx file to its correct location.
    [actuator_bracket.SLDPRT]
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2011-06-03 Updated thermal vias on 12V converter to reduce errors
    [Main.PcbDoc, MarioLib.PcbLib]
2011-06-03 Final gerber files sent to FreeDFM and passed
    [Main.PcbDoc]
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2011-06-10 Added gerbers and re did the motor board
    [Main.PcbDoc, Main.PrjPCB, Main.SchDoc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]
2011-06-11 Fixed up things on motor borad
    Added test points
    Shifted a large capacitor
    Swaped two of the layers
    Committed both boards to free dfm checker at 4pcb.com
    Motor board needs looking at
    Motor baord feedback: https://www.freedfm.com/freedfm/0016816202925768/results/summary2.htm
    Main board passed with no errors
    [Main.PcbDoc, Motor Board.PcbDoc, Motor Board.PrjPcb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]
2011-06-12 Fixed Motor board
    It now passes the free DFM checker on 4pcb.com
    [Main.PrjPCB, Motor Board.PcbDoc, Motor Board.PrjPcb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]
2011-06-12 Added final gerber files for pannels
    All four test have now passed DFM checker. That is:
    * Main PCB
    * Motor Board PCB
    * Panel1
    * Panel2
    Yay!!! Time to order these suckers
    [Panels.PrjPCB]
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2011-06-28 Fixed includes and removed unneeded board.h's
2011-06-28 Major update to the Makefile and src directory.
    Makefile now calculates dependencies automatically.
    No longer are seperate board makefiles needed.
    Added useless main function to all main.c files to prevent make errors.
    Slight problem with all main files needing recompilation when just a
    part of the libs changes. Stupid make won't listen to me.
    [main.c]
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2011-07-04 removed the rest of the errors in the steering code and added some pins to board.h. I also added a line to the makefile so the steering files would compile
    [main.c]
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2011-07-24 tried to get a board to program have made progress but havent got it working
    [config.cfg]
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2011-08-05 Added ground pin for trace and USART1
    Changed the defines so SCK is replaced by a logic 0 pin
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2011-08-08 Fixed all the warning messages
    [main.c, potentiometer.c]
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2011-08-15 Fixed the switch defines to match the schematic
2011-08-15 Changed order to match silk screen
    There is some differences between switchs labels and the silkscreen
    labels. This should be fixed in Altium at some point.
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2011-08-27 BROKEN: Added switches component
    [main.c]
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2011-08-27 Fixed change to switch name
    [main.c]
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2011-08-30 Fixed the stupid link order error from Atmels code.
    Writing to flash and resetting the device now works properly.
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2011-09-02 Fixed the error, don't know why there's a warning as well
    [main.c]
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2011-09-02 Fixed most of the merge errors/warning. HENRY: Last ones are for you.
    [main.c]
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2011-09-02 Simon, you're missing out on Cookie bear choc chip fudge cookies.. You should have stayed at uni.
    [main.c]
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2011-09-03 Fixed the switch names in schematics
    The silk screen names for the test points on the boards are now wrong.
    I have put vivid on the boards to make sure the are not accedently read.
    [Main.PrjPCB, Main.SchDoc, Other.SchDoc]
2011-09-03 Fixed reversed pins for encoder decoder chip
    This needs pushing into the pcb layout, but at least it's now fixed in
    the schematic.
    [Main.PrjPCB, MarioLib.SchLib, Sensors.SchDoc]
2011-09-03 no more build errors
    [main.c]
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2011-09-04 no errors when compiling on my system, fixed the errors from ci joe
    [main.c]
2011-09-04 no errors when compiling on my system, fixed the errors from ci joe. second attempt.
    [main.c]
2011-09-04 no errors when compiling on my system, fixed the errors from ci joe. third attempt.
    [main.c]
2011-09-04 no errors when compiling on my system, fixed the errors from ci joe. fourth attempt.
    [main.c]
2011-09-04 no errors when compiling on my system, fixed the errors from ci joe. fifthattempt.
    [main.c]
2011-09-04 no errors when compiling on my system, fixed the errors from ci joe. sixth attempt.
    [main.c]
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2011-09-04 some alterations specific to testing, also a bug fix
    [main.c]
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2011-09-05 Decoding/encoding packets is possibly broken. msg.command always == 0
    [main.c]
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2011-09-05 more verbose error state transitions
    [main.c]
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2011-09-06 bug fixes, normal transitions work
    [main.c]
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2011-09-07 Fixing `make test` to also test with full TRACE_LEVEL
2011-09-07 Added SPI for the communicating with the student board
    But it doesn't work... Locks up trying to send the message
    [main.c]
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2011-09-08 First crack at the student board SPI code.
    Haven't tried compiling as gcc is still installing
    [main.c]
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2011-09-08 Fixed the build errors
    [board.h, main.c]
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
